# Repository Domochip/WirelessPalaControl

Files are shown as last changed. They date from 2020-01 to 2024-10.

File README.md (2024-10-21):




# WPalaControl

This project uses "Palazzetti library" and a D1 Mini to control Fumis based stove.  
It allows to power On/Off, change the setPoint, change fans speed, get status/alarms/temperatures of the stove.

Native HTTP requests are available which make is fully compatible with all existing Palazzetti/Fumis home automation plugins/apps.

Additionally, this project add MQTT protocol to monitor/control your stove in a much more efficient way.

## Stove Compatibility

Fumis Controller is used by many manufacturer for their stoves.
Here is a non-exhaustive list:  
  
Palazzetti / Jotul / TurboFonte / Godin / Fonte Flamme / Invicta / Casatelli / Alpis / Faizen / HETA / ...

If you have this control panel and/or controller in your stove, it's compatible.  
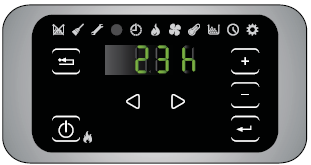
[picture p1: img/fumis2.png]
Fumis Controller
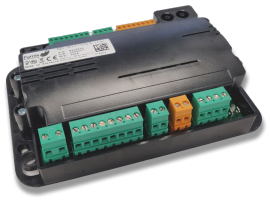
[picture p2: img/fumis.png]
Fumis Controller


## Home Automation compatibility

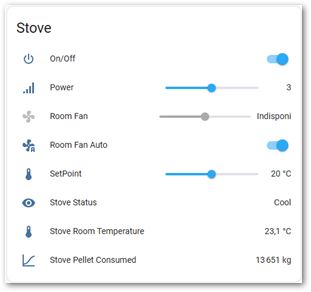
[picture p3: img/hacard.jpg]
hacard
| Logo HASS | [MQTT Integration](https://www.home-assistant.io/integrations/mqtt/) (autodiscovery) |  |
| --- | --- | --- |
| Logo Jeedom | [Palazzetti plugin](https://www.jeedom.com/market/index.php?v=d&p=market_display&id=3104) | Jeedom widget |

## Make/Get your adapter

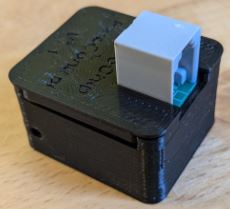
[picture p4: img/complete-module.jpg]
complete Module


🔧 If you want to build it yourself, you can find all details here : [BUILD](BUILD.md) 🔧  

🛍️🚀 Otherwise, I'm producing some small batches and offering it ready to use here : Tindie product (https://www.tindie.com/products/35770/)  

## Connect

⚠️ **You need to use a crossed RJ11 phone cable like this:** ⚠️  
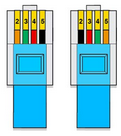
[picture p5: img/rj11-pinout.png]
WPalaControl rj11


Most of stove have an RJ11/RJ12 connector for PalaControl connection.  
If you don't have it, you need to cable it using a splitter to connect screen and PalaControl at the same time :  
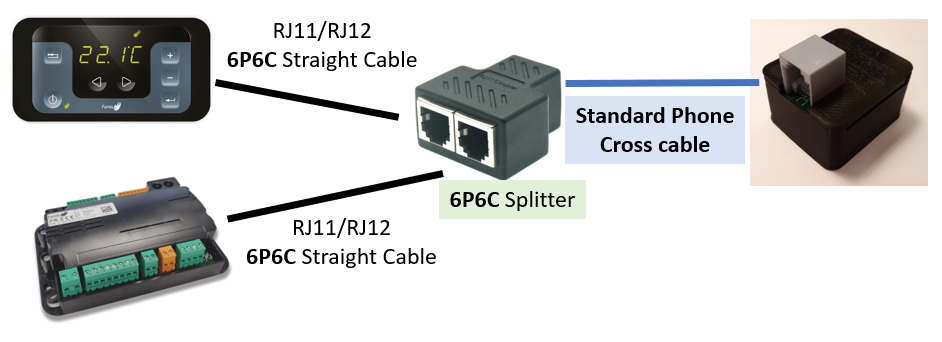
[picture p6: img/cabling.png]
WPalaControl cabling


Splitter and additional cable can be found on Aliexpress (search for "6p6c splitter" and "rj12 cable").  
The splitter should correspond to this small schematic :  
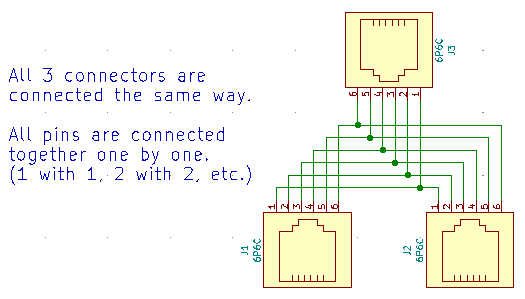
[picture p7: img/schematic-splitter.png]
WPalaControl schematic-splitter


## First Boot

During First Boot, the ESP boot in Access Point Mode

- Network SSID : `WirelessPalaControlXXXX`
- Password : `PasswordPalaControl`
- ESP URL : 👉 http://wpalacontrol.local 👈

Connect to this network and then configure it.

## Configuration pages

### Status

It returns you useful informations about the module and the stove.  
**The stove SN appears then 1 minute later, refreshed stove information appears (default upload period)**  
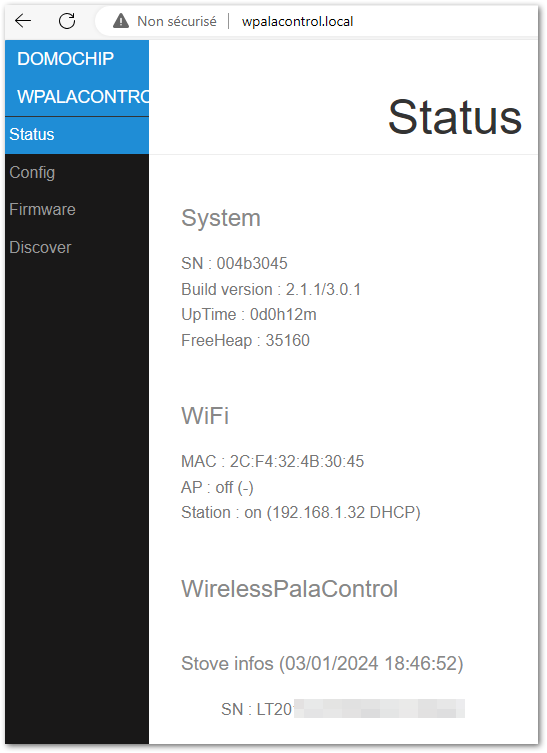
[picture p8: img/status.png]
status screenshot
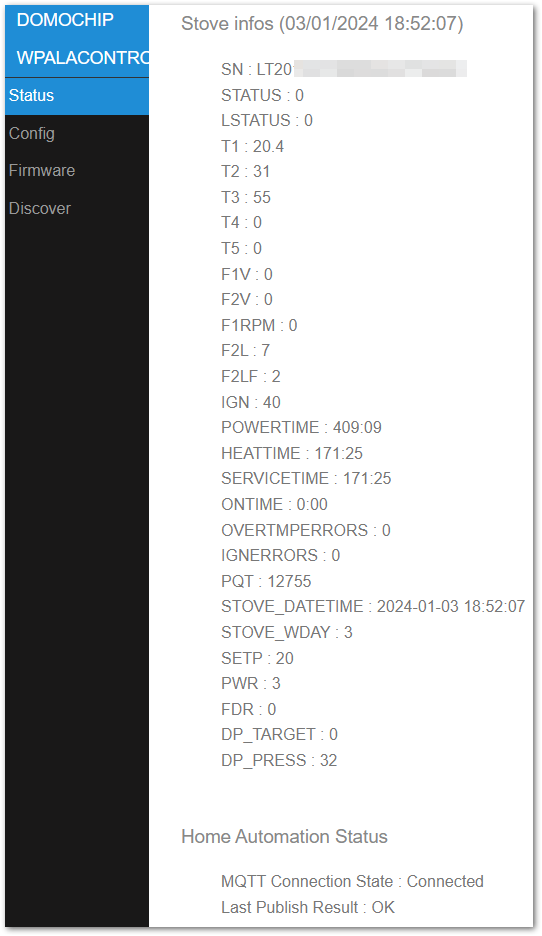
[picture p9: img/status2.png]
status2 screenshot


### Config

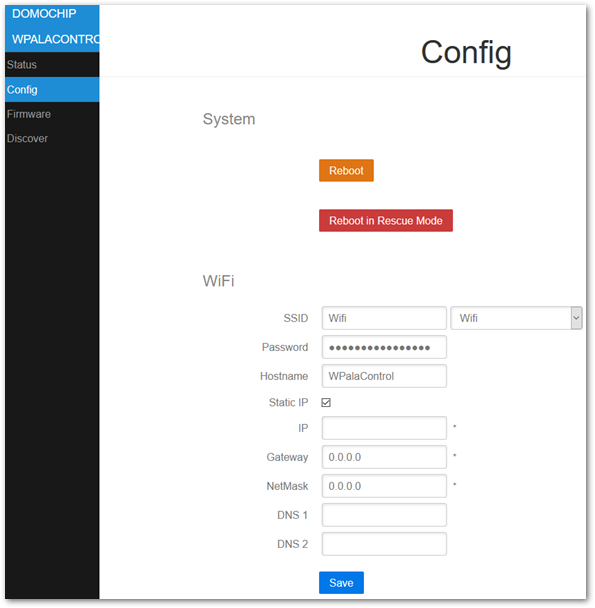
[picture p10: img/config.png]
config screenshot


#### System

- **Reboot**: restart the module
- **Reboot in Rescue Mode**: restart the module with default configuration

#### WiFi

- **ssid & password**: IDs of your Wifi Network  
- **hostname**: name of ESP on the network  
- **IP,GW,NetMask,DNS1&2**: Fixed IP configuration  

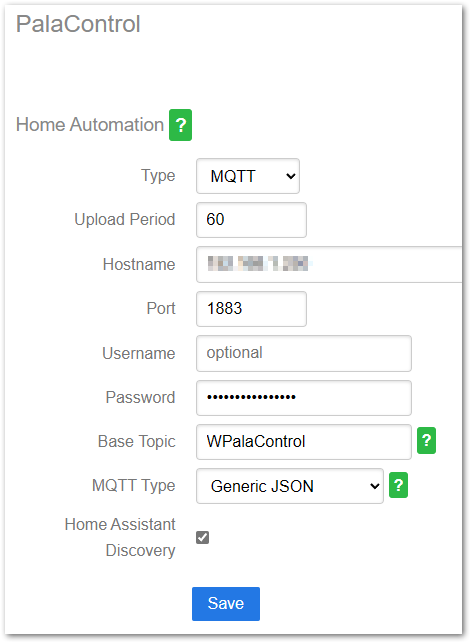
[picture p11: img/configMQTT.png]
configMQTT screenshot


#### PalaControl - Home Automation

- **Type**: enable/disable MQTT communication  
- **Upload Period**: delay between refresh of stove information (in seconds)  
- **Hostname,Port,Username,Password**: MQTT server infos (username and password are - optional)  
- **Base Topic**: prefix used for WPalaControl topic structure  
- **MQTT Type**: defines MQTT topics and data structure: 
  - **Generic**: publish raw values under the base topic (e.g. "{baseTopic}/T1" = "*20.00*")
  - **Generic JSON**: publish values JSON to "category" topic under base topic (e.g. "{baseTopic}/TMPS" = "*{"INFO":{"CMD":"GET TMPS","RSP":"OK......*")
  - **Generic Categorized**: publish raw values to "category" topic under base topic (e.g. "{baseTopic}/TMPS/T1" = "*20.00*")
- **Home Assistant Discovery**: Enable/disable Home Assistant auto-discovery

### Firmware

It allows you to flash a new firmware version using `WPalaControl.*.bin` file:  
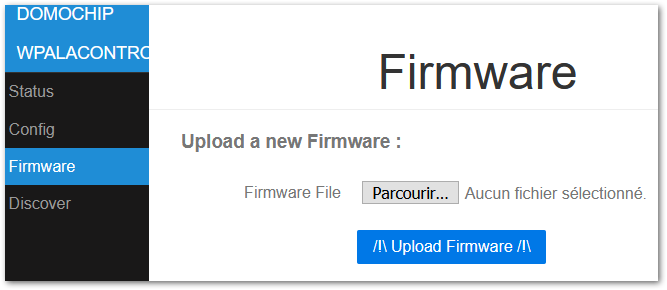
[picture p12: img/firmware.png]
firmware screenshot


## Use it

### HTTP

Natively, HTTP GET request can be sent directly to the module.  
Syntax:  **http://wpalacontrol.local/cgi-bin/sendmsg.lua?cmd={command}**

### MQTT

Commands can be sent via MQTT to %BaseTopic%**/cmd** topic once MQTT is configured.  
Execution result is:

- published following the configured MQTT Type
- published on %BaseTopic%**/result** in JSON format 

Module connection status is published to %BaseTopic%**/connected**:

- 0: not connected
- 1: Module connected but no communication with the stove
- 2: Module and stove connected

### Command List
  
- `GET+STDT`: get static data
- `GET+ALLS`: get all status data
- `GET+STAT`: get status of the stove⏲️
- `GET+TMPS`: get temperatures of the stove⏲️
- `GET+FAND`: get Fan values⏲️
- `GET+SETP`: get current Set Point (desired temperature)⏲️
- `GET+POWR`: get current power (1-5)⏲️
- `GET+CUNT`: get some counters
- `GET+CNTR`: get some counters (same as GET+CUNT)⏲️
- `GET+DPRS`: get delta pressure data⏲️
- `GET+TIME`: get stove clock data⏲️
- `GET+IOPT`: get IO ports status
- `GET+SERN`: get stove Serial Number
- `GET+MDVE`: get stove model and fw version
- `GET+CHRD`: get chrono data
- `GET+PARM+92`: get parameter (ex : 92=pellet type (1-3))
- `GET+HPAR+57`: get hidden parameter (ex : 57=% of pellet to feed for pellet type 3)
- `BKP+PARM+CSV`: get all parameters in a CSV file (HTTP only) ✨
- `BKP+PARM+JSON`: get all parameters in a JSON file (HTTP only) ✨
- `BKP+HPAR+CSV`: get all hidden parameters in a CSV file (HTTP only) ✨
- `BKP+HPAR+JSON`: get all hidden parameters in a JSON file (HTTP only) ✨
- `CMD+ON`: turn stove ON
- `CMD+OFF`: turn stove OFF
- `SET+POWR+3`: set power (1-5)
- `SET+PWRU`: increase power by 1 unit
- `SET+PWRD`: decrease power by 1 unit
- `SET+SETP+20`: set Set Point (desired temperature)
- `SET+STPF+19.8`: set Set Point with a 0.2° precision (depend of your stove model)✨
- `SET+STPU`: increase Set Point by 1 unit
- `SET+STPD`: decrease Set Point by 1 unit
- `SET+RFAN+7`: set Room Fan value (0-5;6=Max;7=Auto)
- `SET+FN2U`: increase Room Fan by 1 unit
- `SET+FN2D`: decrease Room Fan by 1 unit
- `SET+FN3L+0`: set Room Fan 3 value (0-5)
- `SET+FN4L+0`: set Room Fan 4 value (0-5)
- `SET+SLNT+0`: set Silent mode value (0-1)
- `SET+TIME+2023-12-28+19:42:00`: set stove Date and Time (2000-2099) (1-12) (1-31) (0-23) (0-59) (0-59)
- `SET+CSST+0`: set Chrono Status value (0-1)
- `SET+CSTH+2+18`: set Chrono Program Start Hour (1-6) (0-23)
- `SET+CSTM+2+30`: set Chrono Program Start Minute (1-6) (0-59)
- `SET+CSPH+2+22`: set Chrono Program Stop Hour (1-6) (0-23)
- `SET+CSPM+2+45`: set Chrono Program Stop Minute (1-6) (0-59)
- `SET+CSET+2+19`: set Chrono Program Set Point (1-6) (desired temperature)
- `SET+CDAY+7+3+6`: set Chrono Program for week day (Day-Mem-Prog) (1-7) (1-3) (1-6)
- `SET+CPRD+1+19+18+30+22+45`: set Chrono Program data (Prog-Temp-StartH-StartM-StopH-StopM) (1-6) (temperature) (0-23) (0-59) (0-23) (0-59)
- `SET+PARM+92+2`: set parameter 92 to value 2 (ex : 92=pellet type (1-3))
- `SET+HPAR+57+95`: set hidden parameter 57 to value 95 (ex : 57=% of pellet to feed for pellet type 3)

⏲️: Published automatically  
✨: WPalaControl specific commands

### Description

MQTT infos published every "Upload Period":

- `STATUS`: status of the stove
- `LSTATUS`: status of the stove
- `T1`, `T2`, `T3`, `T4`, `T5`: temperature of the stove
- `F1V`, `F2V`, `F2L`, `F2LF`, `F3L`, `F4L`: fan values (meaning depend of your stove model)
- `IGN`: ignition counter
- `IGNERRORS`: ignition error counter
- `POWERTIME`: total heating time (hour:minute)
- `HEATTIME`: ??? (hour:minute)
- `SERVICETIME`: heating time since last maintenance (hour:minute)
- `ONTIME`: time from last power ON (hour:minute)
- `OVERTMPERRORS`: overtemperature error counter
- `STOVE_DATETIME`: date of the stove
- `STOVE_WDAY`: week day of the stove
- `SETP`: current Set Point (desired temperature)
- `PQT`: wood pellet consumption
- `PWR`: current power (1-5)
- `FDR`: feeder
- `DP_TARGET`: delta pressure target
- `DP_PRESS`: actual delta pressure

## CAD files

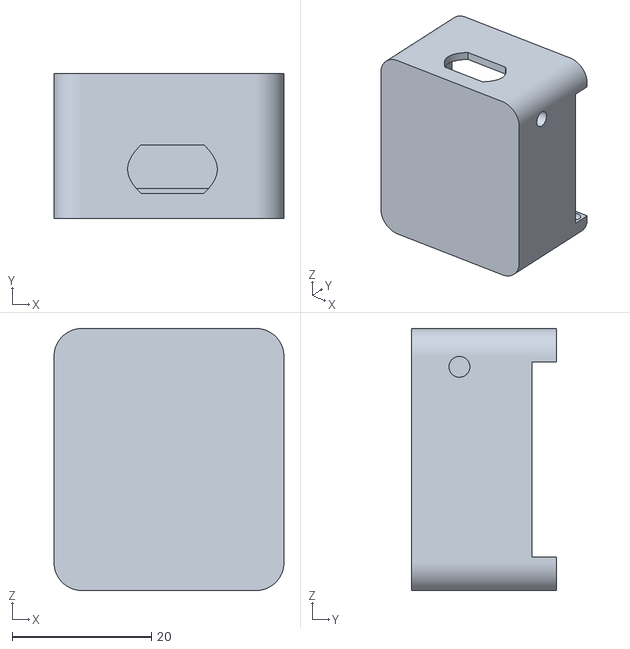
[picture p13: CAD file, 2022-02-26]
box/WirelessPalaControl Box.stl
33.0 x 20.8 x 37.6

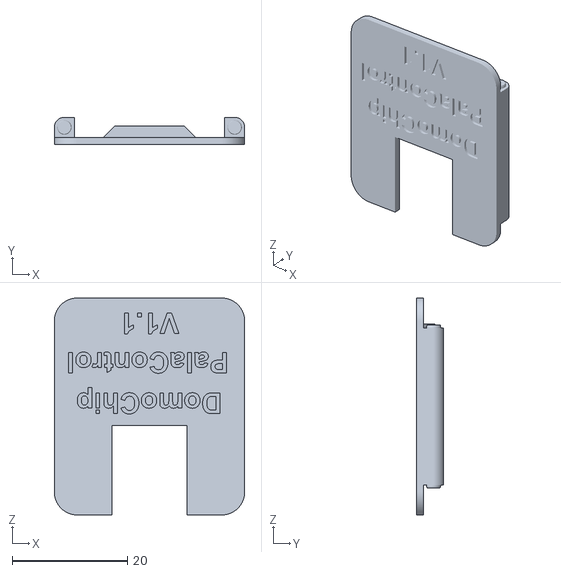
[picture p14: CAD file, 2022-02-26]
box/WirelessPalaControl Lid.stl
33.0 x 4.75 x 37.6

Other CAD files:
box/WirelessPalaControl v10.f3d

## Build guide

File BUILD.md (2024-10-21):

## Build your adapter

This adapter is designed to works with a D1 Mini (ESP8266) but it provides convenient header pins to use it with any other uController.

It is designed by Palazzetti using a Si8621 (Silicon Labs Isolator) to provide electrical isolation between uController and Stove electronic.  
This design uses exact same schematic and components.

### Schematic

All files are inside `schematic` subfolder and has been designed with KiCad (free and open source)  

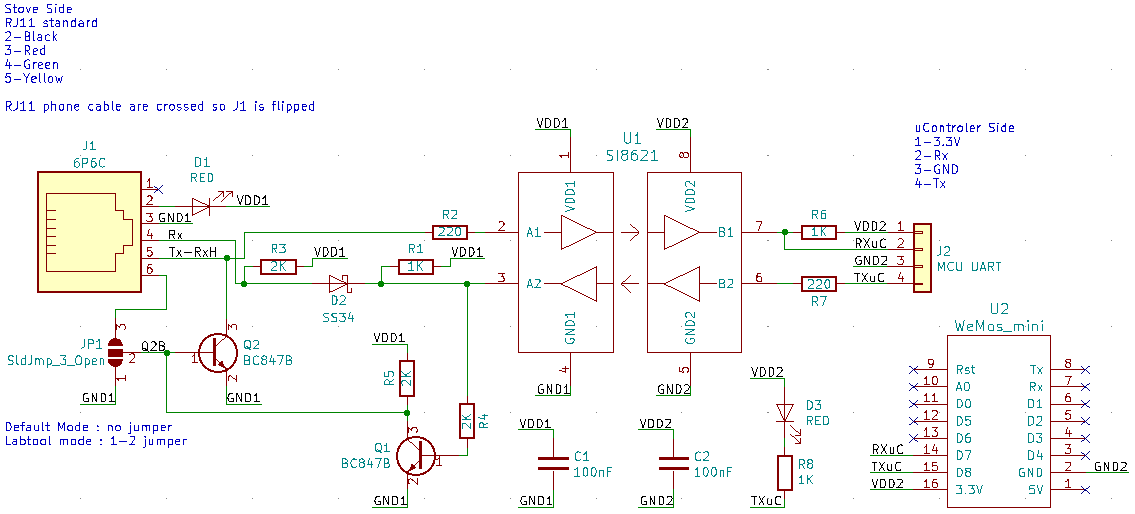
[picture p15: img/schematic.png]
WPalaControl schematic


### PCB

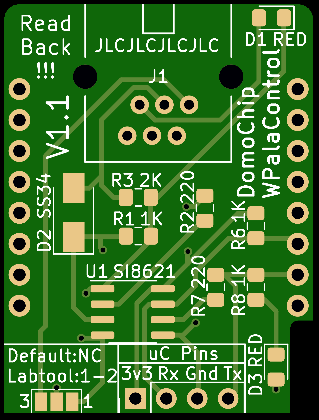
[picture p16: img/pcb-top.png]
WPalaControl PCB Top
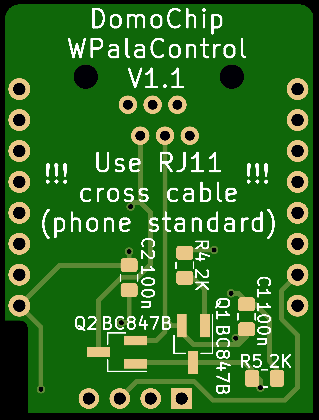
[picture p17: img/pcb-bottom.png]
WPalaControl PCB Bottom
  

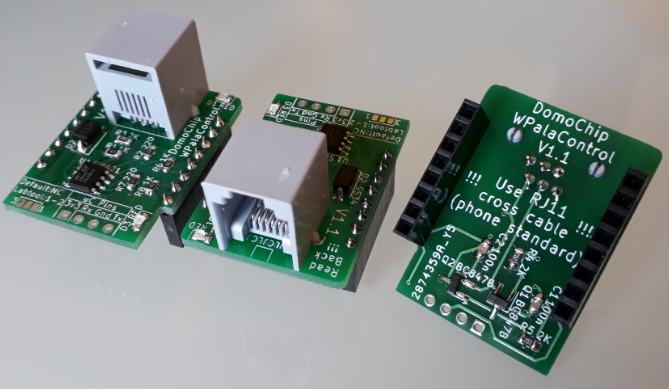
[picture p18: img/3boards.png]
WPalaControl 3boards
  

*I'm producing small batches of this adapter.*  
*If you are interested, you can find it here: [WPalacontrol on tindie](https://www.tindie.com/products/35770/)* 🛍️

### Box

Box project (Fusion 360 & STL) can be found into `box` folder

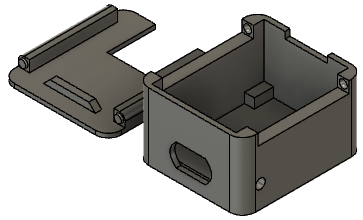
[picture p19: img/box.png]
WPalaControl box


### Firmware

Source code can be compiled using VSCode/PlatformIO and flashed onto a D1 Mini  
Or  
Download latest release in [Release section](https://github.com/Domochip/WPalaControl/releases)

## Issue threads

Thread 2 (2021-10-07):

MQTT and Domoticz

djpostka, 2021-10-07:
Bonjour,

J'ai un soucis pour raccordé la box sur Domoticz, en effet, ce dernier fonctionne avec un système d'IDX,
Pour associé les infos MQTT à mon device virtuel dans domoticz, il faut que le paramétré "IDX" soit intégré à la requête MQTT.

Tasmota ou espEasy offre la possibilité de déclaré l'IDX, serait-ce possible d'ajouter la cela aux paramètre MQTT ?

Merci par avance.

djpostka, 2021-10-09:
J'avoue ne pas vraiment savoir, je ne maitrise pas mqtt en dehors de configurer les clients/serveurs entre eux.
J'ai trouvé cette doc: https://www.domoticz.com/wiki/MQTT

J'ai trouvé ce projet si non qui est conçu pour fonctionner avec la CBOX, mais les commandes semble les même et en lua. Cependant, il n'est plus à jour et ma corrompu ma BDD domoticz sans trop savoir pourquoi.
https://github.com/kinou74/Domoticz-Palazzetti

Domochip, 2022-01-04:
Hello,

La dernière version du firmware rend le WPalaControl compatible.
L'utilisation des plugins conçus pour la CBox doivent maintenant fonctionner avec.
N'hésites pas à me redire si ton problème est solutionné.

djpostka, 2022-01-04:
Bonjour Merci beaucoup pour la mise à jour.
Le plus réussi à communiquer avec le poêle car il me remonte des valeurs correct, mais certaines ne le sont pas comme la vitesse du ventilateur, et je n'ai aucun contrôle sur le poêle (allumage, vitesse ventilateur...).

Voici les logs du plugins lors d'une tentative d'arrêt. Cela semble passé pourtant.

2022-01-05 00:01:08.087 WirelessPalaControl: (WirelessPalaControl) Sending 229 bytes of data
2022-01-05 00:01:08.087 WirelessPalaControl: (WirelessPalaControl) 47 45 54 20 2f 63 67 69 2d 62 69 6e 2f 73 65 6e 64 6d 73 67 GET./cgi-bin/sendmsg
2022-01-05 00:01:08.087 WirelessPalaControl: (WirelessPalaControl) 2e 6c 75 61 3f 63 6d 64 3d 43 4d 44 2b 4f 46 46 20 48 54 54 .lua?cmd=CMD+OFF.HTT
2022-01-05 00:01:08.087 WirelessPalaControl: (WirelessPalaControl) 50 2f 31 2e 31 0d 0a 43 6f 6e 74 65 6e 74 2d 54 79 70 65 3a P/1.1..Content-Type:
2022-01-05 00:01:08.087 WirelessPalaControl: (WirelessPalaControl) 20 74 65 78 74 2f 78 6d 6c 3b 20 63 68 61 72 73 65 74 3d 75 .text/xml;.charset=u
2022-01-05 00:01:08.087 WirelessPalaControl: (WirelessPalaControl) 74 66 2d 38 0d 0a 43 6f 6e 6e 65 63 74 69 6f 6e 3a 20 6b 65 tf-8..Connection:.ke
2022-01-05 00:01:08.087 WirelessPalaControl: (WirelessPalaControl) 65 70 2d 61 6c 69 76 65 0d 0a 41 63 63 65 70 74 3a 20 43 6f ep-alive..Accept:.Co
2022-01-05 00:01:08.087 WirelessPalaControl: (WirelessPalaControl) 6e 74 65 6e 74 2d 54 79 70 65 3a 20 74 65 78 74 2f 68 74 6d ntent-Type:.text/htm
2022-01-05 00:01:08.088 WirelessPalaControl: (WirelessPalaControl) 6c 3b 20 63 68 61 72 73 65 74 3d 55 54 46 2d 38 0d 0a 48 6f l;.charset=UTF-8..Ho
2022-01-05 00:01:08.088 WirelessPalaControl: (WirelessPalaControl) 73 74 3a 20 31 39 32 2e 31 36 38 2e 31 2e 31 35 30 3a 38 30 st:.192.168.1.150:80
2022-01-05 00:01:08.088 WirelessPalaControl: (WirelessPalaControl) 0d 0a 55 73 65 72 2d 41 67 65 6e 74 3a 20 44 6f 6d 6f 74 69 ..User-Agent:.Domoti
2022-01-05 00:01:08.088 WirelessPalaControl: (WirelessPalaControl) 63 7a 2f 31 2e 30 0d 0a 43 6f 6e 74 65 6e 74 2d 4c 65 6e 67 cz/1.0..Content-Leng
2022-01-05 00:01:08.088 WirelessPalaControl: (WirelessPalaControl) 74 68 3a 20 30 0d 0a 0d 0a .. .. .. .. .. .. .. .. .. .. .. th:.0....
2022-01-05 00:01:08.062 Status: User: Admin (IP: 192.168.1.27) initiated a switch command (76/WirelessPalaControl - On-Off/Off)

2022-01-05 00:01:31.098 WirelessPalaControl: (WirelessPalaControl) Sending 230 bytes of data
2022-01-05 00:01:31.098 WirelessPalaControl: (WirelessPalaControl) 47 45 54 20 2f 63 67 69 2d 62 69 6e 2f 73 65 6e 64 6d 73 67 GET./cgi-bin/sendmsg
2022-01-05 00:01:31.098 WirelessPalaControl: (WirelessPalaControl) 2e 6c 75 61 3f 63 6d 64 3d 47 45 54 2b 41 4c 4c 53 20 48 54 .lua?cmd=GET+ALLS.HT
2022-01-05 00:01:31.099 WirelessPalaControl: (WirelessPalaControl) 54 50 2f 31 2e 31 0d 0a 43 6f 6e 74 65 6e 74 2d 54 79 70 65 TP/1.1..Content-Type
2022-01-05 00:01:31.099 WirelessPalaControl: (WirelessPalaControl) 3a 20 74 65 78 74 2f 78 6d 6c 3b 20 63 68 61 72 73 65 74 3d :.text/xml;.charset=
2022-01-05 00:01:31.099 WirelessPalaControl: (WirelessPalaControl) 75 74 66 2d 38 0d 0a 43 6f 6e 6e 65 63 74 69 6f 6e 3a 20 6b utf-8..Connection:.k
2022-01-05 00:01:31.099 WirelessPalaControl: (WirelessPalaControl) 65 65 70 2d 61 6c 69 76 65 0d 0a 41 63 63 65 70 74 3a 20 43 eep-alive..Accept:.C
2022-01-05 00:01:31.099 WirelessPalaControl: (WirelessPalaControl) 6f 6e 74 65 6e 74 2d 54 79 70 65 3a 20 74 65 78 74 2f 68 74 ontent-Type:.text/ht
2022-01-05 00:01:31.099 WirelessPalaControl: (WirelessPalaControl) 6d 6c 3b 20 63 68 61 72 73 65 74 3d 55 54 46 2d 38 0d 0a 48 ml;.charset=UTF-8..H
2022-01-05 00:01:31.099 WirelessPalaControl: (WirelessPalaControl) 6f 73 74 3a 20 31 39 32 2e 31 36 38 2e 31 2e 31 35 30 3a 38 ost:.192.168.1.150:8
2022-01-05 00:01:31.099 WirelessPalaControl: (WirelessPalaControl) 30 0d 0a 55 73 65 72 2d 41 67 65 6e 74 3a 20 44 6f 6d 6f 74 0..User-Agent:.Domot
2022-01-05 00:01:31.099 WirelessPalaControl: (WirelessPalaControl) 69 63 7a 2f 31 2e 30 0d 0a 43 6f 6e 74 65 6e 74 2d 4c 65 6e icz/1.0..Content-Len
2022-01-05 00:01:31.100 WirelessPalaControl: (WirelessPalaControl) 67 74 68 3a 20 30 0d 0a 0d 0a .. .. .. .. .. .. .. .. .. .. gth:.0....

Domochip, 2022-01-04:
S'agit-il du plugin a cette adresse?
https://github.com/kinou74/Domoticz-Palazzetti

djpostka, 2022-01-04:
Oui, c'est bien celui ci

Domochip, 2022-01-05:
J'ai fait des tests de mon coté avec Domoticz et ce plugin.
Le plugin semble buggé malheureusement...
Concernant la temperature, il faut remplacer T5 par T1 dans le plugin.py (TMP_ROOM).
C'est T1 sur la majorité des poeles (sinon chercher MAINTPROBE dans le resultat d'une requete GET+STDT : 0 =>T1; 1=>T2; etc.)

Maintenant le plus gros problème se trouve concernant l'envoi des ordres, il ne fonctionne pas ou peu et crash la DB lorsque l'on redémarre Domoticz.
Si on lance un ordre dès le démarrage de Domoticz, il arrive bien, puis plus rien...
et si on redémarre Domoticz ensuite, DB KO/Domoticz HS :
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

djpostka, 2022-01-05:
Oui, le plugins n'est pas tout jeune et n'a pas reçu de mise à jour depuis un moment. Merci quand même, je vais continuer a utiliser mes script qui fonctionne pas trop mal.

Initialement, ma demande concernait surtout la demande d'un IDX MQTT, comme ont peut avoir sur Esp Easy par exemple

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

https://projetsdiy.fr/domoticz-materiel-capteurs-virtuels-espeasy/

Closed 2022-10-01.

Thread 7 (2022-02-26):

Wifi backup?

Flobul, 2022-02-26:
Sometimes, I reboot my wi-fi router and the Wpalacontrol does not reconnect to my router, it creates its own AP, and never try to reconnect. So I have to reset it manually. I notice only when I try to launch manually... So maybe a few days later.

Maybe adding a second SSID network (fallback)? I the first is unreachable, try the other one?
Or maybe a watchbog: if in AP because SSID network was unreachable, retry in 5 minutes?

Domochip, 2022-02-26:
Very strange, WirelessBase should look back for configured SSID every 60sec (during 20sec).
It does only if there is NO Client currently connected to the AP.
Is it your case?

Flobul, 2022-02-26:
No client connected to the WpalaControl AP.

carmelo42, 2022-08-30:
Same here, when the router is restarted, I can see the the Wpalacontrol AP, but even if no client is connected it does not reconnect to my router. I have to reboot Wpalacontrol.

Domochip, 2022-08-30:
please, ensure that no laptop or mobile phone connect to the module

carmelo42, 2022-08-31:
Yes, you were right ... I've forgotten a laptop used once to configure the module , my bad !
Sorry for the noise.

Flobul, 2022-11-11:
Nevermind, an old phone I used to configure WPalaControl was connecting to it...

Closed 2022-11-11.

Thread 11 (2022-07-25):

Platformio compilation error

carmelo42, 2022-07-25:
Hello !
Just downloaded the repo, and in VScode, on Mac and Linux, I got this :

```
> Executing task: platformio run --environment d1_mini <

Processing d1_mini (framework: arduino; board: d1_mini; platform: espressif8266)
-----------------------------------------------------------------------------------------------------------------------------------------------------------------------
Verbose mode can be enabled via `-v, --verbose` option

warning: Calling missing SConscript without error is deprecated.
Transition by adding must_exist=False to SConscript calls.
Missing SConscript 'src\base\data\prepare_webfiles.py'
File "/Users/carmelo/.platformio/penv/lib/python3.9/site-packages/platformio/builder/main.py", line 186, in <module>
CONFIGURATION: https://docs.platformio.org/page/boards/espressif8266/d1_mini.html
PLATFORM: Espressif 8266 (3.2.0) > WeMos D1 R2 and mini
HARDWARE: ESP8266 80MHz, 80KB RAM, 4MB Flash
PACKAGES:
 - framework-arduinoespressif8266 @ 3.30002.0 (3.0.2)
 - tool-esptool @ 1.413.0 (4.13)
 - tool-esptoolpy @ 1.30000.201119 (3.0.0)
 - toolchain-xtensa @ 2.100300.210717 (10.3.0)
LDF: Library Dependency Finder -> https://bit.ly/configure-pio-ldf
LDF Modes: Finder ~ chain, Compatibility ~ soft
Found 41 compatible libraries
Scanning dependencies...
Dependency Graph
|-- ESPAsyncTCP @ 1.2.2
|-- ESP Async WebServer @ 1.2.3
|   |-- ESPAsyncTCP @ 1.2.2
|   |-- Hash @ 1.0
|   |-- ESP8266WiFi @ 1.0
|   |-- ArduinoJson @ 6.19.4
|-- ESPAsyncUDP @ 0.0.0-alpha+sha.697c75a025
|-- ArduinoJson @ 6.19.4
|-- PubSubClient @ 2.8.0
|-- Palazzetti @ 2.1.0+sha.dc144fd
|-- EEPROM @ 1.0
|-- ESP8266WiFi @ 1.0
|-- LittleFS @ 0.1.0
|-- Ticker @ 1.0
Building in release mode
Compiling .pio/build/d1_mini/src/WirelessPalaControl.cpp.o
Compiling .pio/build/d1_mini/src/base/Application.cpp.o
Compiling .pio/build/d1_mini/src/base/Core.cpp.o
Compiling .pio/build/d1_mini/src/base/MQTTMan.cpp.o
Compiling .pio/build/d1_mini/src/base/Main.cpp.o
Compiling .pio/build/d1_mini/src/base/Utils.cpp.o
Compiling .pio/build/d1_mini/src/base/WifiMan.cpp.o
Generating LD script .pio/build/d1_mini/ld/local.eagle.app.v6.common.ld
In file included from src/base/WifiMan.cpp:1:
src/base/WifiMan.h:4:10: fatal error: ..\Main.h: No such file or directory

*****************************************************************
* Looking for ..\Main.h dependency? Check our library registry!
*
* CLI  > platformio lib search "header:..\Main.h"
* Web  > https://registry.platformio.org/search?q=header:..%5CMain.h
*
*****************************************************************

    4 | #include "..\Main.h"
      |          ^~~~~~~~~~~
In file included from src/base/MQTTMan.cpp:1:
src/base/MQTTMan.h:4:10: fatal error: ..\Main.h: No such file or directory

*****************************************************************
* Looking for ..\Main.h dependency? Check our library registry!
*
* CLI  > platformio lib search "header:..\Main.h"
* Web  > https://registry.platformio.org/search?q=header:..%5CMain.h
*
*****************************************************************

    4 | #include "..\Main.h"
      |          ^~~~~~~~~~~
compilation terminated.
compilation terminated.
In file included from src/base/Application.cpp:1:
src/base/Application.h:4:10: fatal error: ..\Main.h: No such file or directory

*****************************************************************
* Looking for ..\Main.h dependency? Check our library registry!
*
* CLI  > platformio lib search "header:..\Main.h"
* Web  > https://registry.platformio.org/search?q=header:..%5CMain.h
*
*****************************************************************

    4 | #include "..\Main.h"
      |          ^~~~~~~~~~~
In file included from src/base/Core.cpp:1:
src/base/Core.h:4:10: fatal error: ..\Main.h: No such file or directory

*****************************************************************
* Looking for ..\Main.h dependency? Check our library registry!
*
* CLI  > platformio lib search "header:..\Main.h"
* Web  > https://registry.platformio.org/search?q=header:..%5CMain.h
*
*****************************************************************

    4 | #include "..\Main.h"
      |          ^~~~~~~~~~~
compilation terminated.
compilation terminated.
*** [.pio/build/d1_mini/src/base/WifiMan.cpp.o] Error 1
*** [.pio/build/d1_mini/src/base/Core.cpp.o] Error 1
*** [.pio/build/d1_mini/src/base/Application.cpp.o] Error 1
*** [.pio/build/d1_mini/src/base/MQTTMan.cpp.o] Error 1
In file included from src/WirelessPalaControl.cpp:1:
src/WirelessPalaControl.h:5:10: fatal error: base\Utils.h: No such file or directory

********************************************************************
* Looking for base\Utils.h dependency? Check our library registry!
*
* CLI  > platformio lib search "header:base\Utils.h"
* Web  > https://registry.platformio.org/search?q=header:base%5CUtils.h
*
********************************************************************

    5 | #include "base\Utils.h"
      |          ^~~~~~~~~~~~~~
compilation terminated.
*** [.pio/build/d1_mini/src/WirelessPalaControl.cpp.o] Error 1
src/base/Main.cpp:12:10: fatal error: ..\Main.h: No such file or directory

*****************************************************************
* Looking for ..\Main.h dependency? Check our library registry!
*
* CLI  > platformio lib search "header:..\Main.h"
* Web  > https://registry.platformio.org/search?q=header:..%5CMain.h
*
*****************************************************************

   12 | #include "..\Main.h"
      |          ^~~~~~~~~~~
compilation terminated.
*** [.pio/build/d1_mini/src/base/Main.cpp.o] Error 1
===================================================================== [FAILED] Took 1.96 seconds =====================================================================
The terminal process "platformio 'run', '--environment', 'd1_mini'" terminated with exit code: 1.

Terminal will be reused by tasks, press any key to close it.

```

I know I can use the released file, but I like to understand why it fail ;)

Flobul, 2022-07-25:
Prefer windows to compile it.

Directories used in the program are not well recognized in linux/Mac OS.

carmelo42, 2022-07-26:
Thanks !
I don't have any Windows machine available, I will then rely on binary releases ;)

Domochip, 2023-12-29:
Code has been updated to be compiled on non-Windows machine.

carmelo42, 2023-12-29:
Thanks :)

Happy to see this project is still updated :)

Closed 2022-07-26.

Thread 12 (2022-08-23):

D1 Mini communication

KaktuMAN, 2022-08-23:
Hi,
After flashing the ESP8266, everything worked properly, I was able to run PalaControl. But at the moment I attach the ESP to the PCB, nothing happens, I'm unable to start the web ui.
It seems that it's the TX pin that is the source of the problem, do you have an idea of why it's not working ?

Domochip, 2022-08-23:
You need to connect it to your stove. Otherwise some timeout occurs and the module keeps rebooting undefinitly

KaktuMAN, 2022-08-23:
I think it was that, but now the stove give me the error 004 and I still don't have access to the web UI

KaktuMAN, 2022-08-23:
And also, the ESP just blink once

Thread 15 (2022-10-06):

Configuration and infos on TIMER status

1300371, 2022-10-06:
Hello,

I've got a Palazzetti stove and there is a TIMER fonction that you have to turn on if you want to schedule ON/oFF.

Is there a way to get that _TIMER status_ and also to set it ?

Here is a video of the feature: https://www.youtube.com/watch?v=YBgKCtgVSOY

Domochip, 2022-10-06:
Hi, I never used it, but I think this is `Chrono Data`/`Chrono Status` that you are looking for.
And `Chrono Program` is the way to configure its planning.

1300371, 2022-10-06:
BTW, is it possible to forward more data via mqtt ? All these data are availble only via http ? 😕

1300371, 2022-10-10:
Ping @Domochip

1300371, 2022-10-24:
Did read you my second question @Domochip ? Sorry for spam

Domochip, 2023-12-28:
Hello,
Sorry for the very very late reply.
The new V3.0.0 (just released) allows you to get this info via MQTT if you send "GET+CHRD" to cmd topic.
Could you give it a try and let me know if it matches to your needs?

1300371, 2023-12-29:
No problem.
To update, just have to upload the _bin_ firmware file througth the UI ?

Domochip, 2023-12-29:
yes

Domochip, 2024-01-30:
Ping @1300371

1300371, 2024-01-30:
Sorry 😅
As this is winter in France, I want to wait spring to not jeopardize my installation (in case of something goes wrong)

Closed 2024-02-18.

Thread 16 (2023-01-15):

Any chance update code for ESP32 ?

Flobul, 2023-01-15:
Hi.

Sorry to bother, but is there any chance you update this repo for another hardware plateform? (espressif32 instead of espressif8266)
Or maybe a way to use the lib with another system (tasmota, espeasy...)

Domochip, 2023-01-15:
Hi,

mm, regading other systems, it is difficult to respect right timing and listen on UDP + TCP + Web like official box.

For ESP32, I tried a few years ago to port it but Ticker class was missing. It seems to exists now and this option seems possible.
ESP32 Mini are still larger than D1Mini and cost a little more so the right question is Why? Do you see a particular improvement?

Domochip, 2024-09-04:
Hello,

code has been adapted to ESP32 on test-esp32 branch

Domochip, 2024-09-04:
And tested successfully on my side

Flobul, 2024-09-23:
Thank you! Nice job.

I made it work but got some compiling errors in ESP8266:
```
Compiling .pio/build/d1_mini/lib359/ESP8266WiFi/WiFiServerSecureAxTLS.cpp.o
Indexing .pio/build/d1_mini/lib64f/libPubSubClient.a
In file included from src/base/Application.cpp:1:0:
src/base/Application.cpp: In lambda function:
src/base/Application.h:9:41: error: 'using ESP8266WebServer = class esp8266webserver::ESP8266WebServerTemplate<WiFiServer>' has no member named 'keepAlive'
 #define SERVER_KEEPALIVE_FALSE() server.keepAlive(false);
                                         ^
src/base/Application.cpp:165:5: note: in expansion of macro 'SERVER_KEEPALIVE_FALSE'
     SERVER_KEEPALIVE_FALSE()
     ^
src/base/Application.cpp: In lambda function:
src/base/Application.h:9:41: error: 'using ESP8266WebServer = class esp8266webserver::ESP8266WebServerTemplate<WiFiServer>' has no member named 'keepAlive'
 #define SERVER_KEEPALIVE_FALSE() server.keepAlive(false);
                                         ^
src/base/Application.cpp:173:5: note: in expansion of macro 'SERVER_KEEPALIVE_FALSE'
     SERVER_KEEPALIVE_FALSE()
     ^
src/base/Application.cpp: In lambda function:
src/base/Application.h:9:41: error: 'using ESP8266WebServer = class esp8266webserver::ESP8266WebServerTemplate<WiFiServer>' has no member named 'keepAlive'
 #define SERVER_KEEPALIVE_FALSE() server.keepAlive(false);
```

```
Compiling .pio/build/d1_mini/FrameworkArduino/core_esp8266_waveform_pwm.cpp.o
src/WirelessPalaControl.cpp: In member function 'bool WebPalaControl::executePalaCmd(const String&, String&, bool)':
src/WirelessPalaControl.cpp:933:28: error: 'class ESP8266WiFiClass' has no member named 'getHostname'
       data["LABEL"] = WiFi.getHostname();
                            ^
Compiling .pio/build/d1_mini/FrameworkArduino/core_esp8266_wiring.cpp.o
src/WirelessPalaControl.cpp:951:28: error: 'class ESP8266WiFiClass' has no member named 'broadcastIP'
       data["WBCST"] = WiFi.broadcastIP().toString();
```

```
src/WirelessPalaControl.cpp: In member function 'bool WebPalaControl::executePalaCmd(const String&, String&, bool)':
src/WirelessPalaControl.cpp:933:28: error: 'class ESP8266WiFiClass' has no member named 'getHostname'
       data["LABEL"] = WiFi.getHostname();
                            ^
src/WirelessPalaControl.cpp:951:28: error: 'class ESP8266WiFiClass' has no member named 'broadcastIP'
       data["WBCST"] = WiFi.broadcastIP().toString();
                            ^
```

Here are the changes I made to "fix" it:
https://github.com/Flobul/WirelessPalaControl/pull/3/files

Domochip, 2024-09-23:
everything has been merged on WPalaControl master branch and I'm able to compile ESP32 version by just switching to the esp32 env:
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

Do you have a different result?

Flobul, 2024-09-23:
esp8266 (KO):
```
 *  Exécution de la tâche : platformio run

Processing d1_mini (framework: arduino; board: d1_mini; platform: espressif8266)
-------------------------------------------------------------------------------------------------------------------------------------------------------
Library Manager: Installing domochip/Palazzetti#v2.7.3
Unpacking  [####################################]  100%
Library Manager: Palazzetti@2.7.3 has been installed!
Verbose mode can be enabled via `-v, --verbose` option
---- Copying base files ----
----------------------------
--- Converting web files ---
----------------------------
CONFIGURATION: https://docs.platformio.org/page/boards/espressif8266/d1_mini.html
PLATFORM: Espressif 8266 (2023.4.0) > WeMos D1 R2 and mini
HARDWARE: ESP8266 80MHz, 80KB RAM, 4MB Flash
PACKAGES:
 - framework-arduinoespressif8266 @ 2.7.4+9
 - tool-esptoolpy @ 1.40501.0 (4.5.1)
 - toolchain-xtensa @ 2.40802.200502 (4.8.2)
LDF: Library Dependency Finder -> https://bit.ly/configure-pio-ldf
LDF Modes: Finder ~ chain, Compatibility ~ soft
Library Manager: Installing domochip/Palazzetti#v2.7.3
Unpacking 0% 10% 20% 30% 40% 50% 60% 70% 80%
Library Manager: Palazzetti@2.7.3 has been installed!
Found 32 compatible libraries
Scanning dependencies...
Dependency Graph
|-- ArduinoJson @ 7.2.0
|-- PubSubClient @ 2.8.0
|-- EEPROM @ 1.0
|-- ESP8266WebServer @ 1.0
|-- ESP8266WiFi @ 1.0
|-- LittleFS(esp8266) @ 0.1.0
|-- Palazzetti @ 2.7.3
|-- Ticker @ 1.0
|-- ESP8266mDNS @ 1.2
Building in release mode
Compiling .pio/build/d1_mini/src/WirelessPalaControl.cpp.o
Compiling .pio/build/d1_mini/src/base/Application.cpp.o
Compiling .pio/build/d1_mini/src/base/Core.cpp.o
Compiling .pio/build/d1_mini/src/base/MQTTMan.cpp.o
Compiling .pio/build/d1_mini/src/base/Main.cpp.o
Compiling .pio/build/d1_mini/src/base/Utils.cpp.o
Compiling .pio/build/d1_mini/src/base/WifiMan.cpp.o
Generating LD script .pio/build/d1_mini/ld/local.eagle.app.v6.common.ld
Compiling .pio/build/d1_mini/lib075/PubSubClient/PubSubClient.cpp.o
Compiling .pio/build/d1_mini/lib248/EEPROM/EEPROM.cpp.o
Compiling .pio/build/d1_mini/lib359/ESP8266WiFi/BearSSLHelpers.cpp.o
Compiling .pio/build/d1_mini/lib359/ESP8266WiFi/CertStoreBearSSL.cpp.o
Compiling .pio/build/d1_mini/lib359/ESP8266WiFi/ESP8266WiFi.cpp.o
Compiling .pio/build/d1_mini/lib359/ESP8266WiFi/ESP8266WiFiAP.cpp.o
Compiling .pio/build/d1_mini/lib359/ESP8266WiFi/ESP8266WiFiGeneric.cpp.o
Compiling .pio/build/d1_mini/lib359/ESP8266WiFi/ESP8266WiFiGratuitous.cpp.o
Compiling .pio/build/d1_mini/lib359/ESP8266WiFi/ESP8266WiFiMulti.cpp.o
.pio/libdeps/d1_mini/PubSubClient/src/PubSubClient.cpp: In member function 'boolean PubSubClient::publish_P(const char*, const uint8_t*, unsigned int, boolean)':
.pio/libdeps/d1_mini/PubSubClient/src/PubSubClient.cpp:523:19: warning: comparison between signed and unsigned integer expressions [-Wsign-compare]
     return (rc == expectedLength);
                   ^
Compiling .pio/build/d1_mini/lib359/ESP8266WiFi/ESP8266WiFiSTA-WPS.cpp.o
Archiving .pio/build/d1_mini/lib248/libEEPROM.a
Compiling .pio/build/d1_mini/lib359/ESP8266WiFi/ESP8266WiFiSTA.cpp.o
Compiling .pio/build/d1_mini/lib359/ESP8266WiFi/ESP8266WiFiScan.cpp.o
Compiling .pio/build/d1_mini/lib359/ESP8266WiFi/WiFiClient.cpp.o
Compiling .pio/build/d1_mini/lib359/ESP8266WiFi/WiFiClientSecureAxTLS.cpp.o
In file included from src/base/Application.cpp:1:0:
src/base/Application.cpp: In lambda function:
src/base/Application.h:9:41: error: 'using ESP8266WebServer = class esp8266webserver::ESP8266WebServerTemplate<WiFiServer>' has no member named 'keepAlive'
 #define SERVER_KEEPALIVE_FALSE() server.keepAlive(false);
                                         ^
src/base/Application.cpp:165:5: note: in expansion of macro 'SERVER_KEEPALIVE_FALSE'
     SERVER_KEEPALIVE_FALSE()
     ^
src/base/Application.cpp: In lambda function:
src/base/Application.h:9:41: error: 'using ESP8266WebServer = class esp8266webserver::ESP8266WebServerTemplate<WiFiServer>' has no member named 'keepAlive'
 #define SERVER_KEEPALIVE_FALSE() server.keepAlive(false);
                                         ^
src/base/Application.cpp:173:5: note: in expansion of macro 'SERVER_KEEPALIVE_FALSE'
     SERVER_KEEPALIVE_FALSE()
     ^
src/base/Application.cpp: In lambda function:
src/base/Application.h:9:41: error: 'using ESP8266WebServer = class esp8266webserver::ESP8266WebServerTemplate<WiFiServer>' has no member named 'keepAlive'
 #define SERVER_KEEPALIVE_FALSE() server.keepAlive(false);
                                         ^
src/base/Application.cpp:181:5: note: in expansion of macro 'SERVER_KEEPALIVE_FALSE'
     SERVER_KEEPALIVE_FALSE()
     ^
src/base/Application.cpp: In lambda function:
src/base/Application.h:9:41: error: 'using ESP8266WebServer = class esp8266webserver::ESP8266WebServerTemplate<WiFiServer>' has no member named 'keepAlive'
 #define SERVER_KEEPALIVE_FALSE() server.keepAlive(false);
                                         ^
src/base/Application.cpp:189:5: note: in expansion of macro 'SERVER_KEEPALIVE_FALSE'
     SERVER_KEEPALIVE_FALSE()
     ^
src/base/Application.cpp: In lambda function:
src/base/Application.h:9:41: error: 'using ESP8266WebServer = class esp8266webserver::ESP8266WebServerTemplate<WiFiServer>' has no member named 'keepAlive'
 #define SERVER_KEEPALIVE_FALSE() server.keepAlive(false);
                                         ^
src/base/Application.cpp:197:5: note: in expansion of macro 'SERVER_KEEPALIVE_FALSE'
     SERVER_KEEPALIVE_FALSE()
     ^
src/base/Application.cpp: In lambda function:
src/base/Application.h:9:41: error: 'using ESP8266WebServer = class esp8266webserver::ESP8266WebServerTemplate<WiFiServer>' has no member named 'keepAlive'
 #define SERVER_KEEPALIVE_FALSE() server.keepAlive(false);
                                         ^
src/base/Application.cpp:205:5: note: in expansion of macro 'SERVER_KEEPALIVE_FALSE'
     SERVER_KEEPALIVE_FALSE()
     ^
src/base/Application.cpp: In lambda function:
src/base/Application.h:9:41: error: 'using ESP8266WebServer = class esp8266webserver::ESP8266WebServerTemplate<WiFiServer>' has no member named 'keepAlive'
 #define SERVER_KEEPALIVE_FALSE() server.keepAlive(false);
                                         ^
src/base/Application.cpp:221:7: note: in expansion of macro 'SERVER_KEEPALIVE_FALSE'
       SERVER_KEEPALIVE_FALSE()
       ^
src/base/Application.h:9:41: error: 'using ESP8266WebServer = class esp8266webserver::ESP8266WebServerTemplate<WiFiServer>' has no member named 'keepAlive'
 #define SERVER_KEEPALIVE_FALSE() server.keepAlive(false);
                                         ^
src/base/Application.cpp:226:7: note: in expansion of macro 'SERVER_KEEPALIVE_FALSE'
       SERVER_KEEPALIVE_FALSE()
       ^
In file included from src/base/Core.h:5:0,
                 from src/base/Core.cpp:1:
src/base/Core.cpp: In lambda function:
src/base/Application.h:9:41: error: 'using ESP8266WebServer = class esp8266webserver::ESP8266WebServerTemplate<WiFiServer>' has no member named 'keepAlive'
 #define SERVER_KEEPALIVE_FALSE() server.keepAlive(false);
                                         ^
src/base/Core.cpp:84:5: note: in expansion of macro 'SERVER_KEEPALIVE_FALSE'
     SERVER_KEEPALIVE_FALSE()
     ^
Archiving .pio/build/d1_mini/lib075/libPubSubClient.a
src/base/Core.cpp: In lambda function:
src/base/Application.h:9:41: error: 'using ESP8266WebServer = class esp8266webserver::ESP8266WebServerTemplate<WiFiServer>' has no member named 'keepAlive'
 #define SERVER_KEEPALIVE_FALSE() server.keepAlive(false);
                                         ^
src/base/Core.cpp:103:5: note: in expansion of macro 'SERVER_KEEPALIVE_FALSE'
     SERVER_KEEPALIVE_FALSE()
     ^
src/base/Core.cpp: In lambda function:
src/base/Application.h:9:41: error: 'using ESP8266WebServer = class esp8266webserver::ESP8266WebServerTemplate<WiFiServer>' has no member named 'keepAlive'
 #define SERVER_KEEPALIVE_FALSE() server.keepAlive(false);
                                         ^
src/base/Core.cpp:118:5: note: in expansion of macro 'SERVER_KEEPALIVE_FALSE'
     SERVER_KEEPALIVE_FALSE()
     ^
src/base/Core.cpp: In lambda function:
src/base/Application.h:9:41: error: 'using ESP8266WebServer = class esp8266webserver::ESP8266WebServerTemplate<WiFiServer>' has no member named 'keepAlive'
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

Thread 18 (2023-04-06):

Stove infos

Ir0n42, 2023-04-06:
Hi, I have received my controller with 1.4.1 system running.
I have configured it on my network and plug RJ11 on my Palazzetti Monica.
But now, stove info still empty, why? Forgot something?
Thank you

Domochip, 2023-04-06:
Hi,
Could you provide a screenshot of the complete version number.
maybe a picture of the cabling to the stove too.

Thanks

Ir0n42, 2023-04-06:
Yes sure!
![Uploading 97B386A4-6BAB-4EED-9DDF-948B14A84888.jpeg…]()

Ir0n42, 2023-04-06:
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

Ir0n42, 2023-04-06:
![Uploading C96A8E17-DF64-4DAE-9256-6EED3C5654E1.jpeg…]()

Ir0n42, 2023-04-06:
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

Ir0n42, 2023-04-06:
![Uploading D22D207B-CF5C-4F3B-B3B8-6D90F3F0F87A.jpeg…]()

Ir0n42, 2023-04-06:
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

Ir0n42, 2023-04-06:
![Uploading 63EA6B6D-D54F-4FF6-88C7-643DC2CC7C92.jpeg…]()

Ir0n42, 2023-04-06:
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

Domochip, 2023-04-07:
OK,
First I advise to update to the last firmware version.
Next to this one, you should see serial number on the landing page.
With your current version, even if nothing appears, it doesn't mean the module doesn't work.
You can try to query this URL to check : http://**{IP}**/cgi-bin/sendmsg.lua?cmd=GET+STDT

Ir0n42, 2023-04-07:
Ok thank you, I have update it.
Message :
 Stove infos (07/04/2023 10:02:30)
    MSG : Stove communication failed! please check cabling to your stove.
And when I Go to http://{IP}/cgi-bin/sendmsg.lua?cmd=GET+STDT
Message :
{"INFO":{"CMD":"GET STDT","MSG":"Stove communication failed","RSP":"TIMEOUT"},"SUCCESS":false,"DATA":{"NODATA":true}}

Domochip, 2023-04-07:
It seems you have an issue with the cabling.
Does the cable match with the image here ? : https://github.com/Domochip/WirelessPalaControl#connect

Ir0n42, 2023-04-07:
Yes ! It's crossed

Domochip, 2023-04-07:
Then, do you have a picture of your stove motherboard?

Ir0n42, 2023-04-07:
I will open it

Ir0n42, 2023-04-07:
That enouth for you?
![Uploading F349A479-4C50-4215-ADFB-769DBD368CD2.jpeg…]()

Ir0n42, 2023-04-07:
@
![Uploading 18DE64C0-0DCA-4E64-BA39-E1F6593D57F0.jpeg…]()

Ir0n42, 2023-04-07:
![Uploading BB2FE962-0CBC-43A3-BE78-15FA04A11DB2.jpeg…]()

Ir0n42, 2023-04-07:
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

Domochip, 2023-04-07:
Yes, defenitly!
This is a MicroNova motherboard and WirelessPalaControl is **NOT** compatible with MicroNova.
As per written in first chapters (https://github.com/Domochip/WirelessPalaControl), this project aims to control Fumis based stoves.
Your stove should be pretty old to have this kind of Motherboard.

I let you contact me by mail for further discussion.

Closed 2023-04-07.

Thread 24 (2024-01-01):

Status feedback slower than in earlier versions?

sven337, 2024-01-01:
I have not bisected this but, I seem to recall that when I sent CMD +ON to start the stove, I would get immediate status feedback over MQTT.
This was with the firmware you shipped me recently, which I upgraded to 2.1.1/3.0.0.

Now, it seems I have to wait for the next publishTick.
Is this a known consequence of the refactoring?

I would very much appreciate to see the status reflected as soon as it changes, and I think it used to work like that.
Thanks

Domochip, 2024-01-02:
thanks for your feedback.
It was a missing return in Palazzetti Lib (switchOff/On functions).
I've implemented it and use it now in WPalaControl.
The current repo version should solve the problem.
I will release it shortly but feel free to compile and use it now if you need ;-)

sven337, 2024-01-02:
Seems like it's stuck in a reboot loop with that version. I need to investigate.

Domochip, 2024-01-02:
Arg, sorry.
Yes, you can connect it using a micro-usb cable and flash it using VSCode/PlatformIO.
I'll have a look shortly

sven337, 2024-01-02:
Indeed, I just did so (esptool.py write_flash 0x0 /tmp/WirelessPalaControl.v2.1.1-3.0.0.bin), and it's back to normal.
So it seems there's something wrong with your change, but it's not obvious to me what it could be.

Domochip, 2024-01-02:
thanks, I just fixed it :-)

Domochip, 2024-01-02:
I'm back regarding the Status feedback.
I was able to compile and run it without any particular issue. Does libraries are up to date on your side? Which OS are you using?
Anyway, the test is "failing" because Palazzetti lib is now going too fast :-D and returned STATUS is not the "final" one.
I mean when I power ON the stove and temperature is bellow the threshold, it should end up to STATUS 9.
But I'm receiving STATUS 3, which is a transient step to 9...
I'll add a delay before reading of Status to return.

sven337, 2024-01-02:
I am pretty sure that before v2.1.1/3.0.0 the status would update more or less right away. I would click "ON" in home assistant (which I've hooked up to send CMD+ON), and receive a MQTT status update to HEATUP = 9 within 1-2 seconds.

I build on Linux, libraries are up-to-date as far as I know (platformio handles that, right?).

My suggestion, don't add a delay, instead reset the next publishTick so it happens earlier?

Domochip, 2024-01-02:
PlatformIO doesn't update libraries because I didn't specified version for ArduinoJson and PubSubClient. Another point to improve... (maybe also for ESP8266 Arduino version).

The delay will be applied only to CMD+ON/OFF commands.
The whole publishTick is not required for powering on/off the stove. And anyway, lib Palazzetti is now so fast that I'm not sure this will solve the problem :-D
I'm currently testing it.

Domochip, 2024-01-02:
A delay of 500ms is working on my side, but I will do a test session to measure it more precisely. Then I'll be able to apply a "safety" margin

Domochip, 2024-01-04:
OK, I did some tests yesterday on my stove.

Stove ON (send switchOff command):
 - not heating nor fan : STATUS 9->0 took 89ms (3rd getStatus)
 - no fire but FAN is cooling : STATUS 9->10 took 37ms (1st getStatus)
 - heating : STATUS 6->10 took 63ms (2nd getStatus)

Sove OFF (send switchON command):
 - SETP is 2°C under the T1 (no need to heat) : STATUS 0->3 took 37ms (1st getStatus) THEN 3->9 took 305ms (10th getStatus)
 - SETP is above T1 (will heat) : STATUS 0->3 took 37ms AND after 1.2s STATUS is still equals to 3. Stove switch to 4 later after some check etc.

Conclusion :
 - for switchOff, a delay of 200ms should be OK (max measured is 89ms)
 - for switchOn, a delay of 500ms should be OK (max  is 305ms) (regarding the case where the stove need to heat, a STATUS=3 will then be returned and is a correct return value)

Domochip, 2024-01-04:
OK, the issue should be solved now using the latest release : https://github.com/Domochip/WirelessPalaControl/releases/tag/v2.1.2-3.0.2

Regarding compilation on your env : which distro do you use?

sven337, 2024-01-04:
Thank you, I confirm your latest changes fix the problem I was reporting, I now get immediate status updates again.

I build on Archlinux, but I don't think that should cause any problem. In fact I've just produced my own build with your latest change and it works. I don't know what happened but let's ignore it.

Thank you again for your support. By the way, my stove is a Casatelli Carlo.

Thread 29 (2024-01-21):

Set silent mode returns a timeout error

Flobul, 2024-01-21:
Hi.

When SET+SLNT+1 command is sent, the room fan stops, but the cmd returns a timeout issue.
When SET+SLNT+0 command is sent, nothing happens (is it supposed to recover last fan value ?)

```
Mac@Flobul % curl "http://192.168.XXX.XXX/cgi-bin/sendmsg.lua?cmd=SET+SLNT+0"
{"INFO":{"CMD":"SET SLNT","RSP":"OK"},"DATA":{"SLNT":0,"PWR":1,"F2L":0,"F2LF":0},"SUCCESS":true}%

Mac@Flobul % curl "http://192.168.XXX.XXX/cgi-bin/sendmsg.lua?cmd=SET+SLNT+1"
{"INFO":{"CMD":"SET SLNT 1","RSP":"TIMEOUT","MSG":"Stove communication failed"},"DATA":{"NODATA":true},"SUCCESS":false}%
```

Domochip, 2024-01-30:
Hi,

SET+SLNT+1 should not return a timeout error, this is effectively a bug.
Regarding SET+SLNT+0, it does nothing...

I'll have a look at this bug shortly.
thx

Domochip, 2024-02-04:
Hi, Could you give it a try with the latest pre-release?
If the error still occur, I'll need your GET+STDT to understand, what happens.

Flobul, 2024-02-04:
Hi.

```
Mac@Flobul % curl "http://192.168.23.49/cgi-bin/sendmsg.lua?cmd=SET+SLNT+0"
{"INFO":{"CMD":"SET SLNT","RSP":"OK"},"DATA":{"SLNT":0,"PWR":1,"F2L":0,"F2LF":0},"SUCCESS":true}%
Mac@Flobul % curl "http://192.168.23.49/cgi-bin/sendmsg.lua?cmd=SET+SLNT+1"
{"INFO":{"CMD":"SET SLNT 1","RSP":"TIMEOUT","MSG":"Stove communication failed"},"DATA":{"NODATA":true},"SUCCESS":false}%
```

Initial values : FAN OFF and POWER 1. When I send SLNT+1, POWER is set to 3. Nothing happens on SLNT+0.

Domochip, 2024-02-04:
Hi,

First, thank you, following the track, I found a bug I introduced recently (I just fixed the pre-release).
Regarding your issue, The "SILENT" mode seems to be designed for Stove which have FAN3 and FAN4 (additionnal Air ducts or Water pumps).

Here is what it is doing: Set RoomFan, FAN3 and FAN4 to 0
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
Your Stove has FAN2TYPE = 2 which means you have only Room Fan and then iSetRoomFan3Atech return an error.

So for your model, you just need to do a SET+RFAN+0
I will improve error messages of WPalaControl in next release, then it will return an UNSUPPORTED error.

Flobul, 2024-02-04:
You're welcome.

Only ROOM FAN on my stove, exactly.

I just tested your latest fix, same cmd results than before, but now POWER is no more set to 3 anymore.

Closed 2024-02-04.

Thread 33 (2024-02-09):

Add F3L and F4L setting

carmelo42, 2024-02-09:
Just tried the 2.1.5/3.1.2v2 pre-release :

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

It works great :)

I can change the main fan setting (F3L) but there are 2 settings missing : left and right fans (F3L and F4L) :

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

Domochip, 2024-02-09:
Thank you for the feedback.
I had a doubt about this part because my stove doesn't have this additionnal fans.
So, if I understand well, it would be better to have 2 sliders for F3 and F4, right? With value from 0 to 5?

carmelo42, 2024-02-09:
Yes exactly :)
2 sliders for the 2 additional fans, scale 0 to 5.

pm2036, 2024-02-09:
Hello,
On my stove, F3L and F4L is only 0/1. Maybe it depends of the stove model?

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

carmelo42, 2024-02-09:
Mine is "TURBOFONTE TAL" which is I think the same as PALAZZETTI JULIA :

```
// 20240209100452
// http://192.168.0.239/cgi-bin/sendmsg.lua?cmd=SET+FN4L+4

{
  "INFO": {
    "CMD": "SET FN4L",
    "RSP": "OK"
  },
  "DATA": {
    "F4L": 4
  },
  "SUCCESS": true
}
```
On the MQTT bus :
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

And for the other fan :
```
// 20240209100713
// http://192.168.0.239/cgi-bin/sendmsg.lua?cmd=SET+FN3L+4

{
  "INFO": {
    "CMD": "SET FN3L",
    "RSP": "OK"
  },
  "DATA": {
    "F3L": 4
  },
  "SUCCESS": true
}
```
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

pm2036, 2024-02-09:
Ok, mine is a Palazzetti Allegro

`http://192.168.110.70/cgi-bin/sendmsg.lua?cmd=SET+FN3L+4`
`{"INFO":{"RSP":"OK","CMD":"SET FN3L","TS":1707471245},"SUCCESS":true,"DATA":{"F3L":1}}`

I think the max value is in sendmsg.lua?cmd=GET+ALLS
"FANLMINMAX":[0,5,0,1,0,1]

Domochip, 2024-02-09:
Yes, FANLMINMAX contains these limits.
2 firsts numbers are min and max for RoomFan (aka FAN2)
2 nexts are for F3
then 2 last numbers are for F4

So, the good option id to use some switches for stove which have "0,1" limits and sliders for "0,5" limits
I'll implement that shortly

Domochip, 2024-02-09:
V3 prerelease is available and adjust the HomeAssistant Entity type based on the Fan Min and Max values.
Could you let me know if it fit your needs?

carmelo42, 2024-02-09:
It works great :)

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

Domochip, 2024-02-09:
In your case, switch buttons can be removed then

carmelo42, 2024-02-09:
Yes I will remove them.
I'm happy, I've removed https://github.com/marcopal74/home-assistant-palazzetti which was not working every time.

pm2036, 2024-02-09:
Ok for me too, thanks.
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

Closed 2024-02-18.

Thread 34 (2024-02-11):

SET+PWR+2 sent instead of SET+POWR+2

carmelo42, 2024-02-11:
Hello,

From HA, when is use the slider to set fire power to 2, the command sent is SET+PWR+2 instead of SET+POWR+2 so it doesn't change the value:

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

If I send the correct command through HTTP it's ok:
```
// 20240211090505
// http://192.168.0.239/cgi-bin/sendmsg.lua?cmd=SET+POWR+2

{
  "INFO": {
    "CMD": "SET POWR",
    "RSP": "OK"
  },
  "DATA": {
    "PWR": 2,
    "F2L": 2,
    "FANLMINMAX": [
      0,
      5,
      0,
      5,
      0,
      5
    ]
  },
  "SUCCESS": true
}
```

Domochip, 2024-02-11:
thx, I republished the v3 prerelease with to fixed topic

carmelo42, 2024-02-11:
Flashed, and it works fine :)
Thanks a lot :)

Closed 2024-02-11.

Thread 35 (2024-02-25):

Not working on ESP01

Christoffer-da, 2024-02-25:
I tried to flash and run on another esp8266 variant, the esp01.
Unfortunately it flashes well, but won't run.
I get the rst error 4, boot mode 3.7.

Would be nice to be able to use this firmware on the different esp8266 variants. This could also involve the possibility to set rx/tx gpio in the ui.

Christoffer-da, 2024-02-25:
When I get the time, I will try to change the board in platform io, and also the pin-out, to see if I can get everything working.

Domochip, 2024-02-25:
This project has been designed on D1 Mini which is much more convenient than ESP01. What is the benefit to run it on ESP01?

Christoffer-da, 2024-02-25:
For a project that basically only uses rx-tx, the small and cheap esp-01 might be better suited. You do not loose function, and it is way cheaper.
I mostly use the esp32, but for this it would be great to reuse a modbus module I have previously used to control my underfloor heating system.

For me the d1mini is great, and if I do not get it up and running, I might just buy from your tindie shop, for the ease of it.

Closed 2024-03-02.

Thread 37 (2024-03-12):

Add another rj11 connector on the board

Christoffer-da, 2024-03-12:
Just received the board, and now awaiting the last pieces, to be able to install.

I do not know if this is a valid suggestion, but here we go:

If you add another RJ11 connector on the next revision of the board, bridged with the existing one, the we could save one cable and the external rj11 splitter. It would also make your board, baught on Tindie, a drop in component, without the need to buy extra stuff elsewhere.
It woul be nice to just put this board in between the existing connection on the stove controller.

Flobul, 2024-03-27:
Some stoves have a spare RJ11 connector on the back of it.
I wonder, what is the rate of stoves without/with spare RJ11 on the back ?

I think, adding a RJ11 to the board would make it bigger and the board would not fit the size of the ESP8266 Wemos anymore.

Domochip, 2024-09-04:
I agree with @Flobul, there is not so much stove without the rj11 on the back.
Anyway, I documented the Y adapter required and also, I have some in stock too.

Closed 2024-09-04.

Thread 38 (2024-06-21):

MQTT fail after power outage

SlackPhoby, 2024-06-21:
Hi,
Thank you for this great work! Sorry for my English.
I am reporting a bug that occurs after a power outage. The MQTT connection is lost, and 4 out of 6 chips on the same network fail to reconnect. The other 2 chips reconnect successfully. The failing chips require a manual restart to function again.
I have 5 of them connected to the OpenHab MQTT broker. Three of them fail after a power outage, and 1 connected to Home Assistant fails too.
The problem started after upgrading the firmware to 2.1.4. Before that, I was using version 1.4.1, and it worked well.
Thanks again for your work.
Sincerely,
Axel
I hope this is helpful!

Domochip, 2024-06-24:
Hi,
Thanks for your feeback.
Could you let me know which exact version is currently on your module?

Domochip, 2024-06-24:
ok,

For confirmation, you have 5 WPalaControl (and so 5 stoves) on the same Wifi network?
When you got the issue, modules were reconnected to the Wifi and only the MQTT was disconnected?
Did you got any other issue or instability?
Could you let me know what is your MQTT configuration in one of your WPalaControl module?
Does all module are configured the same way?

thanks

SlackPhoby, 2024-06-24:
Hi,
Yes, I have 6 stoves, each with its own wirelespalacontrol device, all on the same network (it's a tourist complex with cabins). I have a single Raspberry Pi with openHAB functioning as an MQTT broker. After a power outage, all of them connect well to the WiFi, but not all connect to the MQTT. All the devices have the same configuration. I think the problem is that the WiFi network comes up faster than the Raspberry Pi with openHAB starts, so they try to connect to an MQTT broker that hasn't started yet, but then they don't try again; they simply remain disconnected. For them to connect, I have to do a manual restart, and then they connect fine.

The strange thing is that before updating the version, it worked well, so I don't think it's a network or device configuration issue since the only thing I changed was updating the firmware. The configuration is exactly the same as it was with version 1.4.1.

Once connected, the devices work perfectly, with no instability or any other issues.

The MQTT configuration is as follows:

Type: MQTT
Upload period: 60
Hostname: [ipbroker]
Port: [1883]
No username
No password
Base topic: $model$
MQTT type: generic

Domochip, 2024-06-30:
Hi,
Sadly, I was not able to repeat the problem on my side.
But I can see only one place where the problem can occur in the code.
In my MQTT Management library, if the MQTT client is not connected, it will always retry to connect, except if a disconnection has been called.
https://github.com/Domochip/WirelessPalaControl/blob/04ef6ba220e5e0dfc10867c8054c544e4dda59ee/src/base/MQTTMan.cpp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

WPalaControl do not disconnect MQTT except during a reboot but if MQTT is configured, a connection is executed just after.
This means that PubSubClient (underlying library to connect to MQTT) should never return a state equals to MQTT_DISCONNECTED.

BUT there is a specific case which switch the state to MQTT_DISCONNECTED even if I don't call disconnection method, here :
https://github.com/knolleary/pubsubclient/blob/2d228f2f862a95846c65a8518c79f48dfc8f188c/src/PubSubClient.cpp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

and then, I can find this issue which is mentionning this code :
https://github.com/knolleary/pubsubclient/issues/927

I so have some new questions for you 😉 :
- what broker are you using and which version of it?
- did you got the problem only during a power outage
- did the problem occured multiple time (did you got multiple outage?)

thanks for your help

SlackPhoby, 2024-07-01:
Hi, yes of course, whatever you need!
Currently, I have 5 stoves connected to Mosquitto MQTT v3 installed on a Raspberry Pi with OpenHAB 3.4. Out of these 5, 3 always fail (I live in a mountainous area with frequent snowfalls, so I have frequent power outages).
The other stove is connected to Mosquitto MQTT v5 (latest version) installed on a Beelink mini PC with Home Assistant (also latest version), and it always fails after a power outage.

The failures occur **only** after a power outage. After a manual restart, they connect perfectly and do not fail. They work perfectly, with no connection errors or command loss, until the next power outage, when they fail again.

Attached is a photo of how the main tab looks after a power outage and another one after restarting and working properly.
After power outage:
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
After reboot, working:
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

Domochip, 2024-09-04:
Hello,
Ok, you are using Mosquitto as Broker but the version number you gave is not the Mosquitto version.
For example, the latest on is 2.0.18 (https://mosquitto.org/download/)
Could you check the version?

SlackPhoby, 2024-09-05:
Hi, yes
On a Raspberry Pi with OpenHAB 3.4

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

On a Beelink mini PC with Home Assistant

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

These are the versions I am currently using and in which this issue persists. thanks

Domochip, 2024-09-05:
ok, I'll try to simulate wifi disconnection with a metal box and I can control an MQTT broker myself

Domochip, 2024-09-07:
Thanks a lot for your patience, I was able to debug it and found the issue.
The latest release fix the problem.

Closed 2024-09-08.

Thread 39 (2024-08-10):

No stove connection during initialization byte 0x201c in iGetStatusAtech function

dxmen7, 2024-08-10:
Hello, I have following issue, I have debugged every single line until Palazzetti.cpp line 1013:
Palazzetti::CommandResult Palazzetti::iGetStatusAtech()
{
    CommandResult cmdRes;
    // die zeile gibt nicht erwarteten wert zurück
    cmdRes = fumisComReadByte(0x201C, &_STATUS);
    if (cmdRes != CommandResult::OK) {
        Serial1.println("fumisComReadByte(0x201C, &_STATUS) != CommandResult::OK");
        return cmdRes;
    }

Here the controller tries to read byte =x201c and expects specifc byte value, but this failed. Without knowledge about Fumis byte structure it's difficult for me to go ahead.
DO you have an idea or more background knowledge about Fumis byte structure?

I have a Fumis Alpha UI from JOTUL stove connected to Fumis controller, where I connected my RJ11 cable to my controller.
If you need further information, please let me know.

Debugged serial Rx/Tx on stove and µC side looks fine.

Domochip, 2024-08-30:
Hello,

What is your motherboard model?

Domochip, 2024-09-04:
I can only imagine 2 scenario :
 - there is a problem with the adapter and/or cable
 - your  motherboard is not compatible

Could you give me more details about your motherboard and explain how you cabled it?

dxmen7, 2024-09-04:
Hello,Thanks for your reply. Yes I will give you my motherboard model number this weekend, I have to partially dismount my stove. I checked the adapter several times with a friend together and measured every single element. In my opinion, there can be a risk with a newer hardware version from Fumis and potentially an incompatibility. On 4. Sep 2024, at 20:52, Domochip ***@***.***> wrote:
I can only imagine 2 scenario :

there is a problem with the adapter and/or cable
your  motherboard is not compatible

Could you give me more details about your motherboard and explain how you cabled it?

—Reply to this email directly, view it on GitHub, or unsubscribe.You are receiving this because you authored the thread.Message ID: ***@***.***>

dxmen7, 2024-09-04:
Sorry,Forgot the second part. Cabled it by RJ11 cable and modified as you described in your repo with crossing the lines.This cable goes to adapter, adapter is on top of D1 Mini and d1 mini Ports also correct.With serial monitor I have checked Rx and Tx on both sides and can see an Tx by D1 Mini after receiving an Rx and vice versa from stove side. On 4. Sep 2024, at 20:52, Domochip ***@***.***> wrote:
I can only imagine 2 scenario :

there is a problem with the adapter and/or cable
your  motherboard is not compatible

Could you give me more details about your motherboard and explain how you cabled it?

—Reply to this email directly, view it on GitHub, or unsubscribe.You are receiving this because you authored the thread.Message ID: ***@***.***>

Domochip, 2024-09-05:
ok, in that case I advise to take some pictures too at the same time you open it ;-)

dxmen7, 2024-09-08:
Hello from Germany,

I was not able to open side panel for direct access to motherboard.
I only have model type, vendor serial number under device model of UI panel at the side of the stove.
Maybe this help you too.
Attached pictures how is the controller cabled to stove.
I will try gonget more information and manual, how to open side panel.

Please find here iCloud Link to pictures, attaching to mail is too big: https://share.icloud.com/photos/012Ni27n0eGaETrfiNwn6vIIw

Best,
Dennis

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

Domochip, 2024-09-08:
Hello,

When you plug the stove to the module without powering the d1mini, do you see the D1 diode blinking (activity of the stove bus)?
does an error appears on the stove screen after 10sec?
Same questions but with the d1mini powered?

dxmen7, 2024-09-08:
Hello,
Yes, LED on stove side is blinking and confirmed with bus analyzer, that Tx and Rx are transmitted and received frames.
D1 mini powered also.
NO error on stove side after 10 sec.

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

Domochip, 2024-09-08:
What's your Jotul stove model? Do you know if Jotul offers a "ConnectionBox" or a module to control it via mobile phone?

dxmen7, 2024-09-08:
It’s Model PF733 from Jotul.
Yes they offer a WiFi connection box with mobile app for one 200€, that was my trigger to try it by myself with your repo.

Service man also have a RJ11 cable with him to control stove via proprietary software provided by Jotul.
Connection box link with Jotul App you can find here: https://intl.jotul.com/sites/importers/files/products/JOTUL_PELLET_CONTROL_Manual_EN.pdf

Stove manual here: https://www.jotul.de/sites/deutsch/files/products/DE%20%20PF733-%20PNMU00049.pdf

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

Domochip, 2024-09-08:
OK, it should definitely be compatible with my module.

few seconds after powering the d1mini, you should see D3 led blinking shortly. Is that the case?

What's appears in the web page?

dxmen7, 2024-09-08:
Yes, D3 LED is blinking shortly after powering up.
Web Page looks like this:
￼
Uptime currently less than 1 min. But also after 5 mins same behavior.

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

Domochip, 2024-09-08:
The webpage image does not appears. could you paste it in github page directly pls
Which firmware are you using?

dxmen7, 2024-09-08:
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
 I am using firmware 2.1.5/3.1.2

Domochip, 2024-09-08:
OK, log is going out of D4 pin at 38400bps
First you can have look at what's logged.

Do you know how to create a platformio/arduinoIDE project and compile it?
if yes, I advidse you to use this very basic example : https://github.com/Domochip/Palazzetti/blob/master/examples/Serial_esp8266/Serial_esp8266.ino
if No, I can compile it for you

dxmen7, 2024-09-08:
Yes I have compiled it with Arduino IDE, but don't get any useful output. tried different Baudrates for serial monitor

Domochip, 2024-09-08:
What output do you get?

Domochip, 2024-09-08:
baudrate is 38400bps

Domochip, 2024-09-08:
the log is coming out of the D4 pin.
you need an additionnal serial adapter connected to GND and D4 to receive the log

dxmen7, 2024-09-08:
yeah was my fault, I will get one and come back to you

Domochip, 2024-09-08:
no problem ;-)

dxmen7, 2024-09-08:
Got it, unfortunately everything failed :(

wSer started
initialize Failed
myPala.getSetPoint failed
myPala.getAllTemps failed
myPala.GetStatus failed

Domochip, 2024-09-08:
do you have a logic analyzer?

dxmen7, 2024-09-08:
A friend of mine yes. What do you need for information?

Domochip, 2024-09-08:
The goal is to monitor exchanges on tx AND rx of the d1mini with real timing.
That's the ultimate solution to debug what's happening.

Another idea would be to log serial from micro-usb port + another adapter on D7.
But it needs to log the precise timing to be able to reconstruct the "discussion"

Domochip, 2024-09-11:
Hello, could you also try to remove R8 resistor or D3 led?

Domochip, 2024-09-11:
also what's your si8621 exact model (2 letters after 8621)?

dxmen7, 2024-09-11:
I have SI8621EC chip. Asked you former time as I ordered these.
One additional hint, I am using white LEDs, tried red ones earlier, but then D1 Mini didn‘t Boot with Adapter because of too high current flow through LED, with white one and slight higher voltage drop, adapter boots fine.

Domochip, 2024-09-12:
thx, I looking for increasing the R8 value to 2Kohms instead of 1K (maybe more will be needed)
Another person reported it in issue #42

dxmen7, 2024-09-14:
Desoldered R8, nothing changes, what do you need exactly for Rx/Tx or what should I try?

dxmen7, 2024-09-14:
I did it and can provide a picture: D0 is RX, D2 is TX. After Reset of D1 mini, Snapshot was created from UART Decoder
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

dxmen7, 2024-09-14:
can also provide PulseView file:
[dxmen7_domo_snapshot_rx_tx_pulseview.zip](https://github.com/user-attachments/files/17002379/dxmen7_domo_snapshot_rx_tx_pulseview.zip)

Domochip, 2024-09-14:
ok, this is exactly what I needed (pulseview file). I will compare it with mine shortly.
First look shows correct behavior but I need to check the answer of the stove.
when stove send a frame starting by 0x00, board can send a frame starting by 0x02 to read data. Stove immediately reply with a frame starting by 0x02 containing the answer

Domochip, 2024-09-18:
Hello, I just had mine connected and compared traces.
Yours:
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
Mine:
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

So, I can tell that you need to check this part:
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
Normally, when uC send something, it should be received back and in you case, nothing come back.

dxmen7, 2024-09-18:
Thanks for explanation! I have an idea.

where does Pin 6 on controller side at RJ12 connector get the power of stove side in your description?
I see in my setup a big mistake, I have a RJ11 cable with RJ11 connector. Thought it was a RJ12 one with 6 wires.

so in theory base of transistor Q1 don‘t get any power to connect.

did you use normal phone cable RJ12 or RJ12 cross over or do it by yourself by cutting and soldering the lines one by one?

Domochip, 2024-09-18:
sorry, I didn't exactly understand what you mean.
As described here : https://github.com/Domochip/WirelessPalaControl#connect
I'm using an RJ11 cable (4 wires) and they are crossed (don't seems to be common in the end)

dxmen7, 2024-09-18:
Okay understood. I have also a RJ11 cable and crossed the wires by myself because didn‘t get online a cross over cable.
with only 4 wires, I don‘t understand, how base of Q2 is powered of Pin 6 by J1?
In your picture, it looks like that out of J1 you have 5 lines, but only 4 are connected to the stove.
when Q2 isn‘t switched up, I think there is the communication problem on my side at the uC.

dxmen7, 2024-09-18:
Ah, now got it.

Domochip, 2024-09-18:
Base of Q2 is powered by R5 or not powered when Q1 is ON
Pin 6 is not used and I don't know its real usage but there was a switch on my original CBox, so I've made this solder jumper for the future if we discover something new.

szengerle, 2024-09-21:
Supported @dxmen7 on hardware level - TL;DR: Q2 was the root-cause
With the knowledge that signal must be looped back to MCU / MCU TX must be on TxRx put the SuT into some test circuit:
- TxRx to high (1MΩ)
- Square TX signal from MCU (signal generator)
- VCC/GND on both sides

Results:
- Q1 is working - feeding square into Q2's base
- Q2's collector is high - no square; 0/5V square on base

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

- 5V Emitter to VCC voltage

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

Replaced Q2:
- Voltage is droping now on base - square also on collector
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

- MCU side Rx shows also looped-back signal
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

@dxmen7 will test later with controller connected

dxmen7, 2024-09-21:
Now communication with stove works, as you said, after 10sec appears communication error on Stove screen with error code E004, is this the correct behaviour?

dxmen7, 2024-09-22:
Solved the last issue, cable was interrupted... now it works!
Thank you so much for your support! How can I donate your work?

Domochip, 2024-09-22:
Cool that it works now 👍
I have a paypal at domochip@hotmail.com

Domochip, 2024-09-22:
Thank you so much for your donation!
This helps me a lot for my home automation and electronics projects.
👍

Closed 2024-09-22.

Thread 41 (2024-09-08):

Stove communication failed

1300371, 2024-09-08:
I use WPalaControl since 3 years now without issues.

Usually, i unplugged (from electric power) the stove and WPala module from winter to automn.
I replugged recently my setup and saw that WPalaControl failed to communicate with stove.

My tries until then:
- check/switch cable
- update firmware from 1.4.1 to 2.2.2

When i plugged the stove to the module, some LED lights up but WPalaControl indicates:
`MSG : Stove communication failed! please check cabling to your stove.`

I changed nothing from last usage...

Is there a way to check logs from WPalaControl ? It's like the module can communicate with stove but info from stove are kind of wrong.

Domochip, 2024-09-08:
If you connect the module to the stove without powering it (micro-usb disconnected), do you see the D1 led blinking (next to the RJ11 connector)?

1300371, 2024-09-08:
Yes

Domochip, 2024-09-08:
The log is going out to the pin D4 on d1_mini. That means you need to solder a cable to a separate serial adapter.

Domochip, 2024-09-08:
otherwise, if you have an ESP32 miniKit like this :
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
Then you can get the log directly to the usb serial of the module

1300371, 2024-09-08:
I use this

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

Domochip, 2024-09-08:
I advise you to check soldering of U1 maybe for a bad contact.
It is usually the difficult point where I'm finally cheking with microscope

1300371, 2024-09-08:
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

Maybe the issue ... Will try to resolder 🤞

1300371, 2024-09-08:
Tricky to sold ... but i was that !!
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
Thank you so much ❤️

Domochip, 2024-09-08:
yw 😉

Closed 2024-09-08.

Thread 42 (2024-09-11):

ESP not booting with Adapter attached

Padm59, 2024-09-11:
When the adapter is connected with the Wemos D1 Mini, it will not boot because pin D8 is pulled high through R8 and LED3.

As described in the Pinout below -> Best Pins to use - ESP8266:
https://randomnerdtutorials.com/esp8266-pinout-reference-gpios/

Quick Fix:
Just desolder R8 and it works.

Domochip, 2024-09-11:
Are you using a RED led too?

Padm59, 2024-09-11:
yes👍

Domochip, 2024-09-11:
what's your si8621 exact model? (two letters after 8621)

Padm59, 2024-09-11:
I have the si8621EC and besides of the following the exact same components.
I still have another connection problem besides the boot problem. This could be my fault though because I used another diode and not the SS34. Mine has a slightly higher forward voltage drop and is probably a bit slower switching.
I do get values and I have control half of the time. It loses the connection every other minute or so. When it looses the connection it only shows an empty serial number.

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

Domochip, 2024-09-22:
Hey,
Did you made some progress? Do you need help?

Padm59, 2024-09-27:
Going to look into it again this weekend, maybe I get my pi pico to work as a logic analyzer.

Padm59, 2024-09-27:
I used the same red LED on the VDD input of the stove, maybe it just has a to high of a voltage drop to work correctly. When connected with the stove, the LED is also flickering all the time. For the power, I guess this could be the problem?
Also doing some sampling of rx and tx on the esp side. Will take a look at them later in detail.

I could try to just remove the LED D1 so that the level shifter and pullups have a higher voltage. tx and rx on the stove side is 5V so why should they be only pulled to roughly 3V or so.

Padm59, 2024-09-27:
[betweenR2andlevelshifter_txstove.zip](https://github.com/user-attachments/files/17169056/betweenR2andlevelshifter_txstove.zip)
[txrxesp_onpagerefresh_stoveconnected_withdata.zip](https://github.com/user-attachments/files/17169057/txrxesp_onpagerefresh_stoveconnected_withdata.zip)

This was recorded the moment after I refresh the webpage and I triggered of the tx channel. I had connection to the stove and also got data back in the web interface after the refresh. Maybe it helps, baudrate was 38400 right?
Also the tx line on the stove side looks really messy, probably because of the very destorted and low VDD line.

Domochip, 2024-09-27:
2 things:
- regarding the schematic, I just reproduced the original one I had, so I don't know why it is powered this way (but is working fine)
- did you changed your diode to a proper SS34?

Padm59, 2024-09-27:
I still have the other diode on the board, but I bridged the LED, and now it's working perfectly fine so far.
I had a glance at the signal, and it looked much better without all the noise.
https://mm.digikey.com/Volume0/opasdata/d220001/medias/docus/3694/B1911USD-20D000114U1930.pdf
That's the red led I removed. So I have no led on the board at the moment.
Doing a longer test tonight to see if there are still any communication errors. We will see tomorrow.

Domochip, 2024-09-28:
I'm using any red led found on aliexpress. I can only advise you to use an SS34 as specified in the schematic...

Padm59, 2024-10-02:
Got my self a SS34 yesterday, and now it works flawlessly. I did put the Red Led on VCC back and also have no noise anymore.
Now we know for sure that you won't get away with just unsing another diode😬
Thank you for your help and advise on this one

Back to the original reason why I opend this issue:

When either the LED3 or R8 are removed, it works. I don't need the led anyways.
Maybe use for R8 2kOhms or higher this could also work.

Closed 2024-10-02.

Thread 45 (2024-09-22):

Découvert impossible dans Home Assistant

Archange2222, 2024-09-22:
Bonjour

J'ai correctement configuré l'ESP et la connexion avec Home Status est OK

> Home Automation Status
> MQTT Connection State : Connected
> Last Publish Result : OK

Cependant Home Assistant ne le détecte pas automatiquement :

Mosquitto broker : 6.4.1
Home Assistant :
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

Merci

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

Domochip, 2024-09-22:
Bonjour,

Pourriez-vous me confirmer que le numéro de série du Poêle apparait sur la page de status (même si ce ne sont que des 0 pour Jotul):
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

Il faut ensuite utiliser "MQTT Explorer" et jeter un œil à ces topics (sont-ils présents):
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

Bonne Soirée

Archange2222, 2024-09-22:
Bonsoir

Le numero de serie apparaît bien

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

Dans MQTT explorer j'ai cela :

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

Domochip, 2024-09-23:
Bonjour,

Dans MQTT Explorer, c'est la partie dans **homeassistant** qui m'intéresse

Domochip, 2024-09-24:
Bonsoir,

Votre problème est-il résolu? Sinon, pourriez-vous me transmettre une capture de la partie **homeassistant** dans MQTT Explorer comme sur ma capture :
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

Archange2222, 2024-09-24:
Bonsoir,

pardon, voilà le bon imprim écran

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

Domochip, 2024-09-24:
ok, le module envoie donc correctement les infos à homeassistant.
Est-ce que les appareils sont bien apparus dans Home Assistant comme ceci (WPalaControl et Stove) :
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

Archange2222, 2024-09-25:
Bonjour

c’est bon il apparaît bien correctement, j’étais persuadé qu’il fallait faire un ajout manuel comme un nouvel appareil. Mais c’est bon il remonte bien et j’ai bien toutes les informations.

Merci pour votre aide et bonne journée

Closed 2024-09-25.

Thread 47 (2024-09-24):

Ventilation arrière

ec0li82, 2024-09-24:
Bonjour
Je viens de recevoir mon module, cela fonctionne, merci.
Sur mon poele (Palazetti Julie), j'ai une sortie arrière pour chauffer une pièce annexe.

J'ai une entité "left fan" qui a été détectée mais ne fonctionne pas (rien ne se passe, enfin si, le log book montre une déconnexion!).
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

J'ai remarqué que mon ventilateur arrière correspond à F4L :

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

Comment faire utiliser cette valeur dans home assistant?

Merci.

Domochip, 2024-09-24:
Bonjour,

Pourriez-vous m'indiquer le modèle de poêle que vous possédez?
Afin de comprendre cette inversion, pourriez-vous me transmettre les résultats des 2 pages web suivantes:
http://wpalacontrol.local/cgi-bin/sendmsg.lua?cmd=GET+STDT
http://wpalacontrol.local/cgi-bin/sendmsg.lua?cmd=GET+ALLS

Merci

ec0li82, 2024-09-24:
Les voici
{"INFO":{"CMD":"GET STDT","RSP":"OK"},"DATA":{"LABEL":"WirelessPalaControl","GWDEVICE":"wlan0","MAC":"34:94:54:8E:28:F3","GATEWAY":"192.168.0.1","DNS":["192.168.0.1"],"WMAC":"34:94:54:8E:28:F3","WMODE":"sta","WADR":"192.168.0.25","WGW":"192.168.0.1","WENC":"psk2","WPWR":"-59 dBm","WSSID":"BLAISE","WPR":"dhcp","WMSK":"255.255.255.0","WBCST":"192.168.0.255","WCH":"11","EPR":"dhcp","EGW":"0.0.0.0","EMSK":"0.0.0.0","EADR":"0.0.0.0","EMAC":"34:94:54:8E:28:F3","ECBL":"down","EBCST":"","APLCONN":1,"ICONN":0,"CBTYPE":"miniembplug","sendmsg":"2.1.2 2018-03-28 10:19:09","plzbridge":"2.2.1 2022-10-24 11:13:21","SYSTEM":"2.5.3 2021-10-08 10:30:20 (657c8cf)","CLOUD_ENABLED":true,"SN":"000000000000000000000000000","SNCHK":0,"MBTYPE":0,"MOD":397,"VER":43,"CORE":130,"FWDATE":"2016-04-18","FLUID":0,"SPLMIN":6,"SPLMAX":51,"UICONFIG":2,"HWTYPE":6,"DSPTYPE":1,"DSPFWVER":29,"CONFIG":2,"PELLETTYPE":2,"PSENSTYPE":0,"PSENSLMAX":0,"PSENSLTSH":0,"PSENSLMIN":0,"MAINTPROBE":4,"STOVETYPE":1,"FAN2TYPE":3,"FAN2MODE":3,"BLEMBMODE":3,"BLEDSPMODE":1,"CHRONOTYPE":0,"AUTONOMYTYPE":1,"NOMINALPWR":9},"SUCCESS":true}

{"INFO":{"CMD":"GET ALLS","RSP":"OK"},"DATA":{"MBTYPE":0,"MAC":"34:94:54:8E:28:F3","MOD":397,"VER":43,"CORE":130,"FWDATE":"2016-04-18","APLTS":"2000-04-07 11:56:13","APLWDAY":7,"CHRSTATUS":0,"STATUS":0,"LSTATUS":0,"SETP":0.00,"PUMP":0,"PQT":12147,"F1V":0,"F1RPM":0,"F2L":2,"F2LF":0,"FANLMINMAX":[0,5,0,5,0,5],"F2V":0,"F3L":0,"F4L":3,"PWR":1,"FDR":0.00,"DPT":0,"DP":67,"IN":13,"OUT":0,"T1":0.00,"T2":20.70,"T3":24.00,"T4":0.00,"T5":20.10,"EFLAGS":0},"SUCCESS":true}

Merci.

Domochip, 2024-09-24:
Bonsoir,

Je viens de faire l'ajustement sur la branche master.
Je vous propose d'essayer cette version du firmware qui doit résoudre votre problème.
[v2.2.2-3.1.5.rc.zip](https://github.com/user-attachments/files/17121453/v2.2.2-3.1.5.rc.zip)

Bonne Soirée

ec0li82, 2024-09-25:
Merci beaucoup ça fonctionne!
J'ai désormais également le setpoint. Celui ci reste a l'état inconnu. Peut être est ce normal si le poêle est éteint ?
Un get fonctionne:
{"INFO":{"CMD":"GET SETP","RSP":"OK"},"DATA":{"SETP":23.00},"SUCCESS":true}

Domochip, 2024-09-25:
Pourriez-vous me donner le contenu de ces topics avec "MQTT Explorer" :
WPalaControl/connected
homeassistant/number/WPalaControl_LT201XXXX_SETP/config
WPalaControl/SETP (attendre 1 minute max pour qu'il arrive)

ec0li82, 2024-09-25:
Bonjour, les voici.
Screenshot pour le 1er et le 3e:

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

Valeur pour le second :

`{"~":"WPalaControl","availability":{"topic":"~/connected","value_template":"{{ iif(int(value) > 0, 'online', 'offline') }}"},"command_template":"SET+SETP+{{ value }}","command_topic":"~/cmd","device":{"configuration_url":"http://wpalacontrol.local","identifiers":["WPalaControl_000000000000000000000000000"],"model":"397","name":"Stove","sw_version":"43 (2016-04-18)","via_device":"WPalaControl_3494548E28F3"},"device_class":"temperature","min":17,"max":23,"mode":"slider","name":"SetPoint","object_id":"stove_setp","state_topic":"~/SET","unique_id":"WPalaControl_000000000000000000000000000_SETP","unit_of_measurement":"°C","value_template":"{{ value_json.SETP }}"}`

Bizarre que je n'ai pas de numéro de serie LT alors que c'est un Palazzeti (après avoir lu d'autres issues, ca devrait etre le cas)?
Mon installateur n'a jamais su me donner de numéro de série quand je lui ai demandé, car Palazetti m'en demandait pour remplacer ma cbox HS.
Je n'ai aucune plaque ni aucun numéro inscrit à l'arrière...

Domochip, 2024-09-25:
ok, coté MQTT, tout est correct. L'entité SetPoint devrait être disponible. Je conseille juste un reboot du WPalaControl pour que ce soit repoussé. Si ça ne fonctionne toujours pas après, il faudra donc que l'on regarde coté HomeAssistant.

Très étrange oui pour le numéro de série. Ce sont bien des 0 pour les Jotul mais pour les poêles Palazzetti, il est sensé être programmé et étiqueté sur le poêle...

ec0li82, 2024-09-25:
OK. j'ai rebooté le wpalacontrol mais meme chose.
En fait l'entité est bien là mais la valeur n'est pas rapportée.
Par exemple via wpalacontrol je vois bien le setp actuellement à 21 (valeur egalement sur le poele)
Par  contre HA lui n'a pas de valeur.
Sur la page web, le slider est au milieu (20 quand je passe avec la souris comme ici) :
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

En cliquant pour voir les details/l'historique, il ne recoit en fait aucune valeur
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

Si je met une valeur en utilisant le slider, le setp est bien appliqué dans wpala et constaté sur le poele. Cependant HA ne l'affiche toujours pas et le slider revient au centre après un refresh.
Si je change la temperature sur le poele, meme chose : le setp est bien recu sur wpala mais pas dans HA.

Je precise que le poele est sous tension mais pas actif, c'est peut etre normal tant qu'il n'est pas "allumé" ?

Domochip, 2024-09-25:
Merci beaucoup pour ces retours précis.
La consigne (aka setPoint) doit remonter même si le poêle est sur OFF.
Vos retours m'ont permis de trouver une erreur dans le code pour la découverte Home Assistant.
Voici donc la version corrigée :
[v2.2.2-3.1.5.rc2.zip](https://github.com/user-attachments/files/17130229/v2.2.2-3.1.5.rc2.zip)

ec0li82, 2024-09-25:
C'est parfait avec cette nouvelle version !
Merci beaucoup !

Domochip, 2024-09-25:
Elle corrige ce problème, mais je viens d'en remarquer d'autres.
La valeur ne se met pas à jour immédiatement.
Je vais améliorer le fonctionnement avec ce mode de publication MQTT

Domochip, 2024-09-28:
Je viens de de faire une pré-release qui améliore tout cela du coup : https://github.com/Domochip/WirelessPalaControl/releases/tag/v2.3.1-3.1.5

ec0li82, 2024-09-28:
Effectivement c'est beaucoup plus réactif !
Merci!

Domochip, 2024-09-28:
;-) de rien

Closed 2024-09-28.

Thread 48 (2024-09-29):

Failure to build related to ArduinoJson - regression

sven337, 2024-09-29:
Hi,
I am unable to build due to the following error:
```
src/base/Application.cpp: In member function 'bool Application::loadConfig()':
src/base/Application.cpp:105:18: error: 'ArduinoJson::V6214PB2::JsonDocument::JsonDocument()' is protected within this context
  105 |     JsonDocument jsonDoc;
      |                  ^~~~~~~
In file included from .pio/libdeps/d1_mini/ArduinoJson/src/ArduinoJson/Document/BasicJsonDocument.hpp:7,
                 from .pio/libdeps/d1_mini/ArduinoJson/src/ArduinoJson/Document/DynamicJsonDocument.hpp:7,
                 from .pio/libdeps/d1_mini/ArduinoJson/src/ArduinoJson.hpp:33,
                 from .pio/libdeps/d1_mini/ArduinoJson/src/ArduinoJson.h:9,
                 from src/base/Application.h:14,
                 from src/base/Application.cpp:1:
.pio/libdeps/d1_mini/ArduinoJson/src/ArduinoJson/Document/JsonDocument.hpp:280:3: note: declared protected here
  280 |   JsonDocument() : pool_(0, 0) {}
      |   ^~~~~~~~~~~~
```

This is a regression introduced by that commit:
```
commit 5165ec0d679e07a6e79a5fa38757287f62cfbb04
Author: DomoChip <domochip@hotmail.com>
Date:   Sat Feb 3 15:03:48 2024 +0100

    Update WirelessBase to 2.1.5

 src/base/Application.cpp | 42 ++++++++++++++----------------------------
 src/base/Application.h   |  2 +-
 src/base/Core.cpp        |  2 +-
 src/base/Core.h          |  2 +-
 src/base/Version.h       |  2 +-
 src/base/WifiMan.cpp     |  2 +-
 src/base/WifiMan.h       |  2 +-
 7 files changed, 20 insertions(+), 34 deletions(-)
```

sven337, 2024-09-29:
My apologies: I have little experience with platformio and did not know I was supposed to "platformio pkg update" first.
This builds fine with an up-to-date ArduinoJson.

Domochip, 2024-09-29:
yes, I'm looking to define the minimum version of ArduinoJson in platformio.ini file

Closed 2024-09-29.

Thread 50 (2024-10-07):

Not responsive after some time

ec0li82, 2024-10-07:
Hello
For the second time, my WirelessPalaControl became unresponsive. This time it's after 4 days. Latest firmware.
Not available/disconnected in ha
Web gui not responding
IP not pinging
RJ11 led stays red as normal
Only solution is replug USB power.

I'm wondering if it's DHCP (ip set in DHCP server)...I've set a static IP directly now...let's see.
Wondering about my USB power source, will change that next time...
How to troubleshoot further?
Thanks.

Domochip, 2024-10-08:
If there is no wifi connection, the module switch automatically to AccessPoint mode.
An interesting thing would be to go close to the module and see if the Wifi network named "WirelessPalaControlXXX" appears

ec0li82, 2024-10-08:
Happened again after 12 hours.
Was not in ap mode.
I've now changed the USB plug and cable. Let's see

ec0li82, 2024-10-14:
Seems stable now... Let's close

Closed 2024-10-14.

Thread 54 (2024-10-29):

Stove communication failed

Palyndiel, 2024-10-29:
Bonjour,

Je n’arrive plus à faire fonctionner le module palacontrol avec mon poêle Turbo Fonte.
Le boîtier fonctionnait encore en début d’année mais en le rebranchant en début de mois, impossible de le faire fonctionner.
J’ai le message d’erreur suivant :
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

Version du module :
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

La petite led rouge est bien allumée :
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

Merci de votre aide.

Domochip, 2024-10-29:
Je vous conseille de contacter le vendeur de votre module dans ce cas

Domochip, 2024-11-01:
Bonsoir,
Avez-vous eu un retour de votre vendeur?

arabine, 2024-11-02:
Bonjour, j'ai exactement le même problème avec un module que je viens d'acheter sur TIndie. Normalement j'ai le bon modèle de poële...

Domochip, 2024-11-02:
@arabine
L'avez-vous acheté auprès de moi?
Si tel est le cas, pourriez-vous plutôt me contacter via Tindie. Je pense que c'est une meilleure option pour suivre le SAV

Bonne Journée

Domochip, 2024-11-02:
Petite clarification:
- Je ne sais pas qui est DIYPala (autre vendeur sur Tindie)
- J'ai ouvert ma boutique Tindie il y a un peu plus d'un mois sous mon pseudo Domochip
- Auparavant, les gens me contactaient par mail et je vendais en direct.
- @Palyndiel : je n'ai jamais fabriqué de PCB blanc. Je n'en suis donc pas le fabricant...
- @arabine : votre nom n'apparait pas dans ma liste de commande. Je ne pense donc pas en être le fabricant non plus.

Malgré tout, le but de ce projet est d'aider les gens à améliorer leur habitat.
Je n'ai pas de soucis à aider tout utilisateur mais pour des problèmes matériels comme les vôtres, il n'y a que 2 options:
- je suis le fabricant : j'assure le SAV
- je ne suis pas le fabricant : c'est à vous de chercher la panne avec mon aide

Si vous n'avez pas de retour de vos fabricant et que vous souhaiter résoudre le problème, n'hésitez pas à donner un maximum de détails (marque et modèle du poêle, année d'achat du WPalaControl, version actuelle du firmware, votre poêle a-t-il une prise accessible ou bien un splitter a dû être ajouté, etc, ...)

@arabine si vous entrez dans ce dernier cas, Il faudra plutôt que vous ouvriez votre propre issue

Bonne Journée

arabine, 2024-11-02:
@Domochip oui mon vendeur est bien DIYPala, je suis entré en contact avec lui il m'a répondu, c'est donc en cours. Si on ne parvient pas à trouver le problème j'ouvre un ticket ici, de tout tracer peut aider les prochaines personnes ayant le même soucis.

(j'ai du matos électronique et je code du firmware donc je peux aider).

Merci !!

Palyndiel, 2024-11-02:
Bonjour, petit retour de mon côté. Après avoir passé 1h à faire du debug dans platformio, et après plusieurs nettoyage/reecriture, le module est tombé en marche.
Donc le matériel fonctionne effectivement mais je pense qu’il y a bien un problème software.

Domochip, 2024-11-02:
Bonjour,
Avez-vous flashé le même firmware plusieurs fois?
Votre poêle est-il ancien? La version du firmware de votre carte Fumis est-elle ancienne? S'agit-il d'une Alpha 65?
Quelle modification software avez-vous faite afin que cela fonctionne?

Palyndiel, 2024-11-03:
Bonjour,
J'ai re-flashé plusieurs fois la version 3.1.11.
Le poêle est récent, modèle Turbo Fonte de 2020.
Aucune modification du firmware, j'ai simplement ajouté des logs pour tenter de debuguer.

J'ai maintenant un nouveau problème, le boitier m'indique qu'il est bien connecté au poêle et à MQTT, mais dans home assistant, la connexion ne cesse de sauté :
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
En gris déconnecté et en jaune connecté.
Du coup le pilotage via HA n'est pas possible. Peut être faut-il ouvrir un autre ticket pour ce problème.

Domochip, 2024-11-03:
Votre poêle a-t-il une prise RJ12 accessible ou bien un splitter a dû être ajouté?
Désolé, mais je persiste à croire à un problème matériel.
Que vous affiche la page web du module durant les périodes "Déconnecté"?

Palyndiel, 2024-11-03:
Oui je suis branché à une prise rj12 accessible directement à l’arrière de l’appareil.
Le module m’affiche toujours connecté, même lorsque je suis déconnecté.

Domochip, 2024-11-03:
Connaissez-vous le modèle de la carte mère de votre poêle?

arabine, 2024-11-03:
Bonjour, j'ai réussi à réparer le module en suivant les conseils du vendeur : comme indiqué ci-dessus, j'ai repassé un coup de fer à souder sur toutes les pattes des composants et ça a fonctionné !

Voilà merci domochip en tout cas pour ta disponibilité et le projet.

Domochip, 2024-11-10:
Bonjour @Palyndiel
J'ai relu ce ticket et j'avais omis un point intéressant:
_Je n’arrive plus à faire fonctionner le module palacontrol avec mon poêle Turbo Fonte. Le boîtier fonctionnait encore en début d’année_

Concernant un problème software:
- de nombreux utilisateurs du WPalaControl ne rencontre pas ce soucis
- si cela fonctionnait bien en début d'année, pourriez-vous retester avec le firmware que vous aviez à ce moment là?
- afin de vérifier que la communication au poêle est opérationnelle, il faut l'interroger: envoyer une commande GET+TMPS par exemple

La source la plus probable du problème reste à mon sens un défaut de soudure sur le si8621.
On appelle ça une soudure sèche (ou aussi soudure collée). Il y a un infime espace entre la patte et la piste sur le PCB. Au début, il y a contact, puis avec le temps, il devient intermittent et finalement il n'y a plus de contact.
La difficulté vient du fait qu'en appuyant sur la patte du composant avec un multimètre pour vérifier la continuité, cela fait contact… puis quand on la relâche le problème revient…
C'est pour cela que je vérifie au microscope que c'est correctement soudé.

Bonne Journée

Palyndiel, 2024-11-12:
Bonjour, la connexion au poêle est stable depuis le 8 novembre. Plus de connexion/déconnexion intempestive. Sans aucune modification de ma part, juste en laissant le module branché.
Je vais néanmoins investir dans un kit de soudure, et essayer de ressouder le composant que vous m’indiquez si jamais je rencontre à nouveau des soucis.
En attendant je clôture le ticket pour ne pas vous embêter plus longtemps.
Merci du temps accordé.

Palyndiel, 2024-11-12:
Bonjour, la connexion au poêle est stable depuis le 8 novembre. Plus de connexion/déconnexion intempestive. Sans aucune modification de ma part, juste en laissant le module branché.
Je vais néanmoins investir dans un kit de soudure, et essayer de ressouder le composant que vous m’indiquez si jamais je rencontre à nouveau des soucis.
En attendant je clôture le ticket pour ne pas vous embêter plus longtemps.
Merci du temps accordé.

Closed 2024-11-12.

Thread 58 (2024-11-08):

SetPoint unknown in Home Assistant

tanc, 2024-11-08:
Hi, I just received my box this morning, nice easy set up, thanks!

The only issue I have is that the SETP isn't registering in Home Assistant and is showing as unknown.
This is what MQTT Explorer says is showing:

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

```
{
  "~": "WPalaControl",
  "availability": {
    "topic": "~/connected",
    "value_template": "{{ iif(int(value) > 0, 'online', 'offline') }}"
  },
  "command_template": "SET+SETP+{{ value }}",
  "command_topic": "~/cmd",
  "device": {
    "configuration_url": "http://wpalacontrol.local",
    "identifiers": [
      "WPalaControl_LT201829880571372127806"
    ],
    "model": "83",
    "name": "Stove",
    "sw_version": "47 (2023-01-30)",
    "via_device": "WPalaControl_3494548E2B82"
  },
  "device_class": "temperature",
  "min": 17,
  "max": 23,
  "mode": "slider",
  "name": "SetPoint",
  "object_id": "stove_setp",
  "state_topic": "~/SETP",
  "unique_id": "WPalaControl_LT201829880571372127806_SETP",
  "unit_of_measurement": "°C",
  "value_template": "{{ value_json.SETP }}"
}
```

Looking at this could it be that the min/max are wrong? This stove is a hydro/boiler model (Ginger Idro 15) so the SetPoint is much higher as its setting the water temperature. Its min is 65 and max 80.

Also `RoomTemp` on this model should be `WaterTemp` with `"name": "Water Temperature",`

Domochip, 2024-11-08:
Hi,

Could you go to this page :
[http://wpalacontrol.local/cgi-bin/sendmsg.lua?cmd=GET+STDT](http://wpalacontrol.local/cgi-bin/sendmsg.lua?cmd=GET+STDT)
and give me the values of:
- FLUID
- SPLMIN
- SPLMAX

tanc, 2024-11-08:
```
"FLUID": 1,
"SPLMIN": 65,
"SPLMAX": 80,
```

Domochip, 2024-11-14:
Could you compile from the master branch and confirm it works fine for you, please

Domochip, 2024-11-15:
It's available in the last release

Closed 2024-11-15.

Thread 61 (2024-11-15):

Feature request: Expose the firebox temp to Home Assistant

tanc, 2024-11-15:
For my nerdy graph needs it would be great to expose the T3 temp to Home Assistant so that I can monitor the relationship between the tank temp and the firebox temp.

```
{
    "INFO": {
        "CMD": "GET TMPS",
        "RSP": "OK"
    },
    "DATA": {
        "T1": 71.9, <-- Tank or outflow temp
        "T2": 63.9, <-- Inflow temp
        "T3": 210, <-- Firebox temp
        "T4": 0,
        "T5": 18 <-- Room temp
    },
    "SUCCESS": true
}
```

Domochip, 2024-11-16:
It's added in the current master branch as a disabled by default one

BorisNanev, 2024-11-16:
"T3": 210, <-- Firebox temp is important for monitoring how stove works and when exhaust gases go too much UP is indicator that your stove is for cleaning (i mean inside of waste box).

tanc, 2024-11-16:
> It's added in the current master branch as a disabled by default one

Should I be able to see it and enable it in Home Assistant already? Or do you mean it needs to be enabled in code first?

BorisNanev, 2024-11-16:
i cant see it in HA. only in browser of domochip.

Domochip, 2024-11-17:
@BorisNanev It is in master branch not part of the current release. You need to compile and flash it in your module if you want to see it

@tanc it will be created in Home Assistant but you'll need to go to the device and enable this entity, then you'll be able to use it like any other

Domochip, 2024-11-17:
going to the stove device, you can find some grayed out sensors, and enable them :
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

BorisNanev, 2024-11-17:
I know, I enabled all sensors in home assistant but I don't have T3. I can a see it in browser but not in hove assistant .

Domochip, 2024-11-17:
You'll find the version containing these new sensors in the latest pre-release (3.4.0)
https://github.com/Domochip/WPalaControl/releases

BorisNanev, 2024-11-17:
That's awesome. Thanks one more time. I was looking for this from years. :)

Domochip, 2024-11-19:
@tanc @BorisNanev Does everything looks good for you?
I'm considering switch the current pre-release as release

BorisNanev, 2024-11-19:
I don't have any issues with pre-release. Everything works perfectly. I do have some random disconnects for 2-3 seconds 3-4 time per day, same as stable release.(I think it's not from bad WiFi connection coz router and device show good connection). It's not big of deal for me.

Domochip, 2024-11-20:
@BorisNanev thank you for the feeback.
Regarding the disconnection, I have it sometime and sometime not (3 days without it on my side now...)
I was not able to catch it yet.
Could you confirm me this behavior :
 - in Home assistant, both Stove and WPalaControl connectivity disconnect and reconnect
 - in WPalaControl webpage, the UpTime is not resetted

BorisNanev, 2024-11-20:
Yes, I can confirm. 35 hours without disconnection. I didn't check UpTime but I will next time.

Domochip, 2024-11-20:
ok, I'll close this issue.
Regarding the disconnection, it is still very hard to figure out now.
I'll have a look at this later when I've time.

tanc, 2024-11-21:
Sorry I wasn't able to test, but just wanted to say thanks, I did the update today and can confirm the fluegas sensor is now available (after enabling it)

Closed 2024-11-20.

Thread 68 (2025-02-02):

WPalaControl unstable

abcklaus, 2025-02-02:
Hi,

I am using the WPalaControl with Palazzetti "Marianne" stove. For any reason the WPalaControl seems to be unstable.

The uptime in the status indicates that the device is restarting. In this example the uptime is about 2h. Actually the last power cycle is about 20h ago ...

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

In Home Assistant I am using the Palazzetti integration. Also here I am observing availability issues:

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

I other issues I have seen that the power supply may be a problem. But after trying three different power supplies I am pretty sure that this is not the root cause.

Any Idea what I can do?

Thanks

Michael

Domochip, 2025-02-03:
Hi,

This may happen if there is some Wifi connectivity issue.
What is the percentage next to your wifi network in Config page?

abcklaus, 2025-02-03:
It’s 58%. Distance between access point and Domochip is about 5m.

abcklaus, 2025-02-03:
ok, thank you. I didn't expect that the quality of the wifi connection may cause issues like that.

In the meantime I did some tweaks in my environment and will observe.

abcklaus, 2025-02-06:
I did some tweaks in my wifi environment. The quality is now between 90 and 100%

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

Today in the morning (07:40) I see that the uptime is again just 2h. Means that the device has restarted at about 05:00

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

Is the wifi connection still an issue?

Domochip, 2025-02-07:
Hi,

Before going more in technical research, is it possible for you to use the MQTT integration (native for this module)?
I want to clarify if that come from HTTP endpoints or not

abcklaus, 2025-02-07:
ok, no problem. I have deactivated the Palazzetti integration in HomeAssistant and activated the MQ integration.

abcklaus, 2025-02-11:
The MQTT Integration is active for some days now.

But there is no improvement. The uptime is still just some hours. The max value I have seen is 1d.

In HA the stove becomes unavailable from time to time.

Domochip, 2025-02-23:
Hi,

Sorry I was off these last two weeks.
mm, sounds like an hardware problem.
Which WPalaControl HW version do you have (1.1 or 2.0) (it's written on the box and on the PCB).
Did you build it yourself or bought it ready to use and where?

abcklaus, 2025-02-23:
Hi,

I am using Version 2.0.

Domochip, 2025-03-03:
Have you bought it from me or from DIYPala?

abcklaus, 2025-03-04:
I bought it from you. Order number is  #515307

Domochip, 2025-03-05:
ok
Do you see a kind of pattern of the restart?
Next steps would be to monitor via USB from a computer and flash some test firmware (going deeper then).
Is it something you are comfortable with? otherwise a return/refund is always possible.

abcklaus, 2025-03-06:
Hi,
yes, flashing some firmware is no problem. I am familiar with that.

I have here an Lolin D1 mini from another project. What do you think - is it worth to flash your firmware to check if the issue is located in the other D1 mini?

Domochip, 2025-03-06:
yes, can be a good first test.

abcklaus, 2025-03-06:
I used a Lolin D1 Mini v4.0. I have compiled and flashed the firmware with vscode/platform io. For and reason this device seems not to be compatible. As soon as i have connected my stove, the stove Shows the error E0004.
So I moved back to the original D1 mini.

abcklaus, 2025-03-07:
ok, found the reason why my D1 mini is not working. The pins are soldered on the other side of the board.

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

abcklaus, 2025-03-07:
ok, found a workaround ;-)

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

Let's see how the new D1 mini will behave ...

abcklaus, 2025-03-22:
During the last days I have monitored the device. Unfortunately switching the D1mini did not help. I am observing the instability. In most cases the device does not have an uptime larger than several hours.

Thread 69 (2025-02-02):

Stove im Home Assistant

abcklaus, 2025-02-02:
Hi,

I am using the WPalaControl with Palazzetti "Marianne" stove. I am using WPalaControl with Palazzetti integration in Home Assistant.

I have observed that the stove becomes unavailable in HA if the target temperature is change while the stove is powered off:

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

Is that behavior intended?

Thanks

Michael

Domochip, 2025-02-03:
Hi,

Do you mean the target temperature is changed directly on the stove physically or via HA?

abcklaus, 2025-02-03:
It happens when I change the target temp in HA.

Domochip, 2025-02-03:
Interesting,
could you give it a try directly using HTTP command and check that it disconnect or not (ex: set target temperature to 20):
http://{WPalaControlIP}/cgi-bin/sendmsg.lua?cmd=SET+SETP+20

abcklaus, 2025-02-03:
Response for HTTP command:

{"INFO":{"CMD":"SET SETP","RSP":"OK"},"DATA":{"SETP":20.00},"SUCCESS":true}

One more thing: When setting the temp in HA I get this error:

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

abcklaus, 2025-02-03:
After executing the HTTP command WPalaControl remains available. But it takes some seconds (approximately 10s) to reflect the change in HA.

Ok, I will contact dotav.

Domochip, 2025-02-03:
For the 10sec delay, it is normal, Palazzetti integration is using HTTP endpoints and no notification is sent from WPalaControl nor CBox using this protocol.
What's interesting is that HA didn't considered the WPalaControl has disconnected, so yes, the problem is coming from Palazzetti integration

dotvav, 2025-02-03:
Hi there. It could be that the response payload from WPalaControl has a
format that I was not expecting. If the processing throws an exception
(missing attribute, unexpected type...) then the device will be reported as
unavailable, until it responds again with something that fulfills the
expectations. Which could be 10s. I haven't had a chance to test today, but
I have some doubts about SETP returning a float value instead of an int.
I'll check tomorrow.

Le lun. 3 févr. 2025, 16:35, Domochip ***@***.***> a écrit :

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

Domochip, 2025-02-03:
Nice trail found. If my memory is good, some stove are able to be configured with 0.2°C step, but in that case, i don't know what CBox returns...

Domochip, 2025-03-05:
@dotvav were you able to confirm if it comes from the float returned?

dotvav, 2025-03-05:
Hi, I came back from vacation last week and haven't found the time to run these tests. I will look into that in the coming days.

dotvav, 2025-03-09:
I ran some tests today, both on the HA integration and on the API lib, and the `float` type of SETP does not cause any issues.

@abcklaus, can you open an issue on the HA Core Github? It will get assigned to me. I don't want to polute Domochip's repo. Feel free to link to this issue and share the tests that you have performed. Also, any error message ort information you can get from the HA logs would be very helpful.

abcklaus, 2025-03-09:
ok, done.

#140215

Thanks

dotvav, 2025-03-10:
@Domochip below is the relevant error from @abcklaus's logs. There is a imeout error when I call `GET STDT`. Do you think that it is possible that the WPalaControl could struggle with concurrent http requests if HA is calling `GET STDT` right after (or during) the `SET SETP` command? (I'll also try to understand why I call `GET STDT` at this point)

````
2025-03-09 18:16:44.569 ERROR (MainThread) [homeassistant.components.palazzetti] Communication error
Traceback (most recent call last):
  File "/usr/local/lib/python3.13/site-packages/aiohttp/connector.py", line 1116, in _wrap_create_connection
    sock = await aiohappyeyeballs.start_connection(
           ^^^^^^^^^^^^^^^^^^^^^^^^^^^^^^^^^^^^^^^^
    ...<5 lines>...
    )
    ^
  File "/usr/local/lib/python3.13/site-packages/aiohappyeyeballs/impl.py", line 73, in start_connection
    sock = await _connect_sock(
           ^^^^^^^^^^^^^^^^^^^^
    ...<6 lines>...
    )
    ^
  File "/usr/local/lib/python3.13/site-packages/aiohappyeyeballs/impl.py", line 208, in _connect_sock
    await loop.sock_connect(sock, address)
  File "/usr/local/lib/python3.13/asyncio/selector_events.py", line 641, in sock_connect
    return await fut
           ^^^^^^^^^
asyncio.exceptions.CancelledError

The above exception was the direct cause of the following exception:

Traceback (most recent call last):
  File "/usr/local/lib/python3.13/site-packages/aiohttp/client.py", line 703, in _request
    conn = await self._connector.connect(
           ^^^^^^^^^^^^^^^^^^^^^^^^^^^^^^
        req, traces=traces, timeout=real_timeout
        ^^^^^^^^^^^^^^^^^^^^^^^^^^^^^^^^^^^^^^^^
    )
    ^
  File "/usr/local/lib/python3.13/site-packages/aiohttp/connector.py", line 548, in connect
    proto = await self._create_connection(req, traces, timeout)
            ^^^^^^^^^^^^^^^^^^^^^^^^^^^^^^^^^^^^^^^^^^^^^^^^^^^
  File "/usr/local/lib/python3.13/site-packages/aiohttp/connector.py", line 1056, in _create_connection
    _, proto = await self._create_direct_connection(req, traces, timeout)
               ^^^^^^^^^^^^^^^^^^^^^^^^^^^^^^^^^^^^^^^^^^^^^^^^^^^^^^^^^^
  File "/usr/local/lib/python3.13/site-packages/aiohttp/connector.py", line 1411, in _create_direct_connection
    raise last_exc
  File "/usr/local/lib/python3.13/site-packages/aiohttp/connector.py", line 1380, in _create_direct_connection
    transp, proto = await self._wrap_create_connection(
                    ^^^^^^^^^^^^^^^^^^^^^^^^^^^^^^^^^^^
    ...<7 lines>...
    )
    ^
  File "/usr/local/lib/python3.13/site-packages/aiohttp/connector.py", line 1113, in _wrap_create_connection
    async with ceil_timeout(
               ~~~~~~~~~~~~^
        timeout.sock_connect, ceil_threshold=timeout.ceil_threshold
        ^^^^^^^^^^^^^^^^^^^^^^^^^^^^^^^^^^^^^^^^^^^^^^^^^^^^^^^^^^^
    ):
    ^
  File "/usr/local/lib/python3.13/asyncio/timeouts.py", line 116, in __aexit__
    raise TimeoutError from exc_val
TimeoutError

The above exception was the direct cause of the following exception:

Traceback (most recent call last):
  File "/usr/local/lib/python3.13/site-packages/pypalazzetti/client.py", line 402, in _execute_command
    async with self._session.get(request_url) as response:
               ~~~~~~~~~~~~~~~~~^^^^^^^^^^^^^
  File "/usr/local/lib/python3.13/site-packages/aiohttp/client.py", line 1425, in __aenter__
    self._resp: _RetType = await self._coro
                           ^^^^^^^^^^^^^^^^
  File "/usr/local/lib/python3.13/site-packages/aiohttp/client.py", line 707, in _request
    raise ConnectionTimeoutError(
        f"Connection timeout to host {url}"
    ) from exc
aiohttp.client_exceptions.ConnectionTimeoutError: Connection timeout to host http://10.60.20.10/cgi-bin/sendmsg.lua?cmd=GET+STDT

The above exception was the direct cause of the following exception:

Traceback (most recent call last):
  File "/usr/src/homeassistant/homeassistant/components/palazzetti/config_flow.py", line 31, in async_step_user
    await client.connect()
  File "/usr/local/lib/python3.13/site-packages/pypalazzetti/client.py", line 48, in connect
    r = await self._execute_command(
        ^^^^^^^^^^^^^^^^^^^^^^^^^^^^
    ...<2 lines>...
    )
    ^
  File "/usr/local/lib/python3.13/site-packages/pypalazzetti/client.py", line 409, in _execute_command
    raise CommunicationError("API communication error") from ex
pypalazzetti.exceptions.CommunicationError: API communication error
`````

Domochip, 2025-03-10:
That's interesting.
Could be a good idea that I give it a try because we are currently working on a reliability problem with @abcklaus .
To clarify things, the first post mention that this problem occurs when changing the temperature (setPoint) while the stove is off.
Does it also happens when the stove is on?

@dotvav  Even if this is something you can fix, I want to give it a try to understand if this is a memory shortage or a "simple" watchdog timeout. (I can improve things for watchdog timeout)

abcklaus, 2025-03-10:
Yes, the issue occurs only if the stove is turned off.

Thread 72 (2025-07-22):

F4L does not appear in Home Assistant via MQTT

quenting57, 2025-07-22:
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

Hi,

My stove has a ducted output. When I physically change the fan speed of the ducted output on the stove, the F4L value updates correctly on the web interface.

However, F4L does not appear in Home Assistant via MQTT, unlike other controls such as temperature, power level, etc.

I’d like to integrate this F4L value into Home Assistant like the other MQTT entities.
Is it possible to expose it, or is there a specific configuration needed?

I’ve attached two screenshots:
	•	Home Assistant interface (F4L missing)
	•	Stove’s web interface (F4L visible and updating)

Thanks!

quenting57, 2025-07-28:
I have noticed that the F4L value is properly published in the MQTT topic PalazettiControl/FAND in JSON format, for example :
`{"F1V":0,"F2V":0,"F1RPM":0,"F2L":2,"F2LF":0,"F3S":0.00,"F4S":0.00,"F3L":0,"F4L":5}`

quenting57, 2025-07-28:
Meanwhile, my Home Assistant solution :

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

And synchronized with a Home Assistant input_number using automations.
**We need to find out why F4L wasn’t automatically discovered by Home Assistant**.

Domochip, 2025-07-31:
The only condition for FAN4 to appear is: FAN2TYPE > 2
This is true in your case, so something is weird here
if you connect to your MQTT broker using MQTT Explorer, do you find a retained message on a topic like : homeassistant/number/WPalaControl_LTXXXX_FAN4 OR homeassistant/switch/WPalaControl_LTXXXX_FAN4?

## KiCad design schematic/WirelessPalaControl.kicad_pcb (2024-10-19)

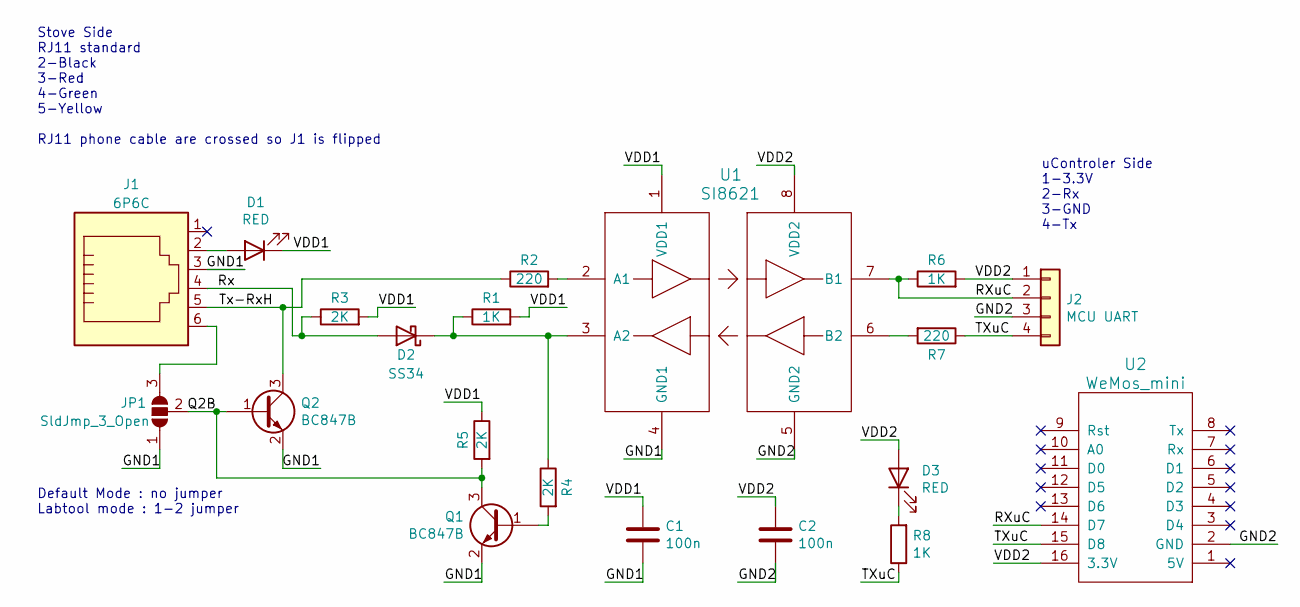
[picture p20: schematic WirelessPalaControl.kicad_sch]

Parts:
C1, C2: 100n; C_0805_2012Metric_Pad1.15x1.40mm_HandSolder
D1, D3: RED; LED_0805_2012Metric_Pad1.15x1.40mm_HandSolder
D2: SS34; D_SMA
J1: 6P6C; Ali_RJ12
J2: MCU UART; PinHeader_1x04_P2.54mm_Vertical
JP1: SldJmp_3_Open; SolderJumper-3_P1.3mm_Open_Pad1.0x1.5mm_NumberLabels
Q1, Q2: BC847B; SOT-23_Handsoldering
R1, R6, R8: 1K; R_0805_2012Metric_Pad1.15x1.40mm_HandSolder
R2, R7: 220; R_0805_2012Metric_Pad1.15x1.40mm_HandSolder
R3, R4, R5: 2K; R_0805_2012Metric_Pad1.15x1.40mm_HandSolder
U1: SI8621; SOIC-8_3.9x4.9mm_P1.27mm
U2: WeMos_mini; wemos-d1-mini-DIL-only

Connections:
/GND1: C1.2, J1.3, JP1.1 (A), Q1.2 (E), Q2.2 (E), U1.4 (GND1)
/GND2: C2.2, J2.3, U1.5 (GND2), U2.2 (GND)
/Q2B: JP1.2 (C), Q1.3 (C), Q2.1 (B), R5.2
/RXuC: J2.2, R6.1, U1.7 (B1), U2.14 (D7)
/Rx: D2.2 (A), J1.4, R3.1
/TXuC: J2.4, R7.1, R8.1, U2.15 (D8)
/Tx-RxH: J1.5, Q2.3 (C), R2.1
/VDD1: C1.1, D1.1 (K), R1.2, R3.2, R5.1, U1.1 (VDD1)
/VDD2: C2.1, D3.2 (A), J2.1, R6.2, U1.8 (VDD2), U2.16 (3.3V)
unnamed: D1.2 (A), J1.2
unnamed: D2.1 (K), R1.1, R4.1, U1.3 (A2)
unnamed: D3.1 (K), R8.2
unnamed: J1.6, JP1.3 (B)
unnamed: Q1.1 (B), R4.2
unnamed: R2.2, U1.2 (A1)
unnamed: R7.2, U1.6 (B2)

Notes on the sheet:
uControler Side 1-3.3V 2-Rx 3-GND 4-Tx
Default Mode : no jumper Labtool mode : 1-2 jumper
Stove Side RJ11 standard 2-Black 3-Red 4-Green 5-Yellow RJ11 phone cable are crossed so J1 is flipped

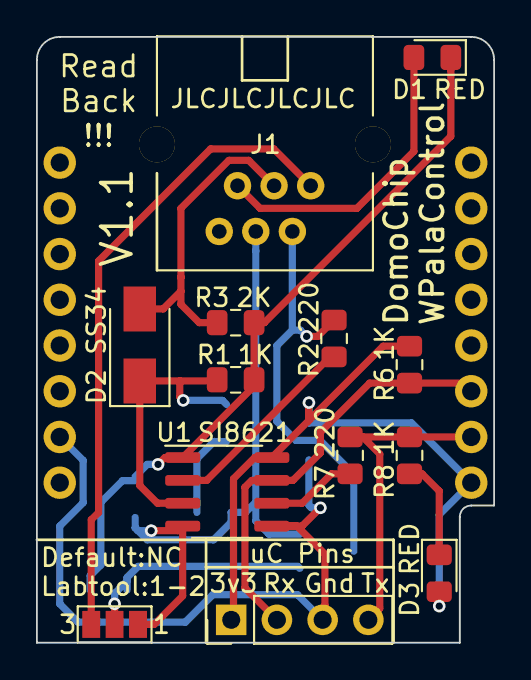
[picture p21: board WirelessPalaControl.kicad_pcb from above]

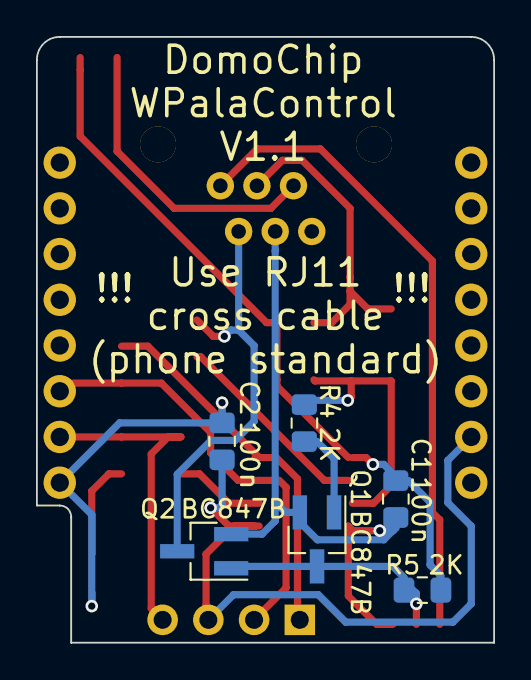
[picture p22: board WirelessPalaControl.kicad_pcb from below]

Board: 2 copper layers, 25.4 x 33.7 mm, 20 parts (7 on the bottom side), 16 nets.

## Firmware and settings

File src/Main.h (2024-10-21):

#ifndef Main_h
#define Main_h

#include <Arduino.h>

// Helper macros to convert a define to a string
#define STRINGIFY(x) #x
#define TOSTRING(x) STRINGIFY(x)

// ----- Should be modified for your application -----
#define APPLICATION1_MANUFACTURER "Domochip"
#define APPLICATION1_MODEL "WPalaControl"
#define APPLICATION1_CLASS WPalaControl
#define VERSION_NUMBER "3.1.11"

#define APPLICATION1_NAME TOSTRING(APPLICATION1_CLASS)     // stringified class name
#define APPLICATION1_HEADER TOSTRING(APPLICATION1_CLASS.h) // calculated header file "{APPLICATION1_NAME}.h"
#define DEFAULT_AP_SSID APPLICATION1_NAME                  // Default Access Point SSID "{APPLICATION1_NAME}{4 digits of ChipID}"
#define DEFAULT_AP_PSK APPLICATION1_NAME "Pass"            // Default Access Point Password "{APPLICATION1_NAME}Pass"

// Control EventSourceMan code (To be used by Application if EventSource server is needed)
#define EVTSRC_ENABLED 1
#define EVTSRC_MAX_CLIENTS 2
#define EVTSRC_KEEPALIVE_ENABLED 0

// Enable developper mode (SPIFFS editor)
#define DEVELOPPER_MODE 0

// Log Serial Object
#ifdef ESP8266
#define LOG_SERIAL Serial1
#else
#define LOG_SERIAL Serial
#endif
// Choose Log Serial Speed
#define LOG_SERIAL_SPEED 38400

// Choose Pin used to boot in Rescue Mode
// #define RESCUE_BTN_PIN 2

// Define time to wait for Rescue press (in s)
// #define RESCUE_BUTTON_WAIT 3

// Status LED
// #define STATUS_LED_SETUP pinMode(XX, OUTPUT);pinMode(XX, OUTPUT);
// #define STATUS_LED_OFF digitalWrite(XX, HIGH);digitalWrite(XX, HIGH);
// #define STATUS_LED_ERROR digitalWrite(XX, HIGH);digitalWrite(XX, HIGH);
// #define STATUS_LED_WARNING digitalWrite(XX, HIGH);digitalWrite(XX, HIGH);
// #define STATUS_LED_GOOD digitalWrite(XX, HIGH);digitalWrite(XX, HIGH);

// construct Version text
#if DEVELOPPER_MODE
#define VERSION VERSION_NUMBER "-DEV"
#else
#define VERSION VERSION_NUMBER
#endif

#endif

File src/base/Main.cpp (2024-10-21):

#ifdef ESP8266
#include <ESP8266WiFi.h>
#include <ESP8266WebServer.h>
using WebServer = ESP8266WebServer;
#else
#include <WiFi.h>
#include <WebServer.h>
#endif
#include <EEPROM.h>
#include <LittleFS.h>
#include <FS.h>

#include "Version.h"
#include "../Main.h"
#include "Application.h"
#include "Core.h"
#include "WifiMan.h"

// include Application header file
#include APPLICATION1_HEADER

// WebServer
WebServer server(80);
// flag to pause application Run during Firmware Update
bool pauseApplication = false;
// variable used by objects to indicate system reboot is required
bool shouldReboot = false;

// System
Core core('0', "Core");

// WifiMan
WifiMan wifiMan('w', "WiFi");

// Application1 object
APPLICATION1_CLASS application1('1', APPLICATION1_NAME);

//-----------------------------------------------------------------------
// Setup function
//-----------------------------------------------------------------------
void setup()
{
#ifdef LOG_SERIAL
  LOG_SERIAL.begin(LOG_SERIAL_SPEED);
  LOG_SERIAL.println();
  LOG_SERIAL.println();
  LOG_SERIAL.flush();
#endif

#ifdef STATUS_LED_SETUP
  STATUS_LED_SETUP
#endif
#ifdef STATUS_LED_ERROR
  STATUS_LED_ERROR
#endif

#ifdef LOG_SERIAL
  LOG_SERIAL.print(F(APPLICATION1_MANUFACTURER " " APPLICATION1_MODEL " "));
  LOG_SERIAL.println(VERSION);
  LOG_SERIAL.println(F("---Booting---"));
#endif

#ifndef RESCUE_BUTTON_WAIT
#define RESCUE_BUTTON_WAIT 3
#endif

  bool skipExistingConfig = false;

  // look into EEPROM for Rescue mode flag
  EEPROM.begin(4);
  skipExistingConfig = EEPROM.read(0) != 0;
  if (skipExistingConfig)
    EEPROM.write(0, 0);
  EEPROM.end();

#ifdef RESCUE_BTN_PIN
  // if config already skipped, don't wait for rescue button
  if (!skipExistingConfig)
  {
#ifdef LOG_SERIAL
    LOG_SERIAL.print(F("Wait Rescue button for "));
    LOG_SERIAL.print(RESCUE_BUTTON_WAIT);
    LOG_SERIAL.println(F(" seconds"));
#endif

    pinMode(RESCUE_BTN_PIN, (RESCUE_BTN_PIN != 16) ? INPUT_PULLUP : INPUT);
    for (int i = 0; i < 100 && skipExistingConfig == false; i++)
    {
      if (digitalRead(RESCUE_BTN_PIN) == LOW)
        skipExistingConfig = true;
      delay(RESCUE_BUTTON_WAIT * 10);
    }
  }
#endif

#ifdef LOG_SERIAL
  if (skipExistingConfig)
  {
    LOG_SERIAL.println(F("-> RESCUE MODE : Stored configuration won't be loaded."));
  }
#endif
#ifdef ESP8266
  if (!LittleFS.begin())
#else
  if (!LittleFS.begin(true))
#endif
  {
#ifdef LOG_SERIAL
    LOG_SERIAL.println(F("/!\\   File System Mount Failed   /!\\"));
    LOG_SERIAL.println(F("/!\\ Configuration can't be saved /!\\"));
#endif
  }

  // Init Core
  core.init(skipExistingConfig);

  // Init WiFi
  wifiMan.init(skipExistingConfig);

  // Init Application
  application1.init(skipExistingConfig);

#ifdef LOG_SERIAL
  LOG_SERIAL.print(F("Start WebServer : "));
#endif
  core.initWebServer(server, shouldReboot, pauseApplication);
  wifiMan.initWebServer(server, shouldReboot, pauseApplication);
  application1.initWebServer(server, shouldReboot, pauseApplication);

  server.begin();
#ifdef LOG_SERIAL
  LOG_SERIAL.println(F("OK"));

  LOG_SERIAL.println(F("---End of setup()---"));
#endif
}

//-----------------------------------------------------------------------
// Main Loop function
//-----------------------------------------------------------------------
void loop(void)
{

  // Handle WebServer
  server.handleClient();

  if (!pauseApplication)
  {
    application1.run();
  }

  wifiMan.run();

  if (shouldReboot)
  {
#ifdef LOG_SERIAL
    LOG_SERIAL.println("Rebooting...");
    delay(100);
    LOG_SERIAL.end();
#endif
    ESP.restart();
  }
}

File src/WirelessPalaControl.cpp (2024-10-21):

#include "WirelessPalaControl.h"

#ifdef ESP8266
#define PALA_SERIAL Serial
#else
#define PALA_SERIAL Serial2
#endif

// Serial management functions -------------
int WPalaControl::myOpenSerial(uint32_t baudrate)
{
#ifdef ESP8266
  PALA_SERIAL.begin(baudrate);
  PALA_SERIAL.pins(15, 13); // swap ESP8266 pins to alternative positions (D7(GPIO13)(RX)/D8(GPIO15)(TX))
#else
  PALA_SERIAL.begin(baudrate, SERIAL_8N1, 23, 5); // set ESP32 pins to match hat position (IO23(RX)/IO5(TX))
#endif
  return 0;
}
void WPalaControl::myCloseSerial()
{
  PALA_SERIAL.end();
  // set TX PIN to OUTPUT HIGH to avoid stove bus blocking
#ifdef ESP8266
  pinMode(15, OUTPUT);
  digitalWrite(15, HIGH);
#else
  pinMode(5, OUTPUT);
  digitalWrite(5, HIGH);
#endif
}
int WPalaControl::mySelectSerial(unsigned long timeout)
{
  size_t avail;
  unsigned long startmillis = millis();
  while ((avail = PALA_SERIAL.available()) == 0 && (startmillis + timeout) > millis())
    ;

  return avail;
}
size_t WPalaControl::myReadSerial(void *buf, size_t count) { return PALA_SERIAL.read((char *)buf, count); }
size_t WPalaControl::myWriteSerial(const void *buf, size_t count) { return PALA_SERIAL.write((const uint8_t *)buf, count); }
int WPalaControl::myDrainSerial()
{
  PALA_SERIAL.flush(); // On ESP, Serial.flush() is drain
  return 0;
}
int WPalaControl::myFlushSerial()
{
  PALA_SERIAL.flush();
  while (PALA_SERIAL.read() != -1)
    ; // flush RX buffer
  return 0;
}
void WPalaControl::myUSleep(unsigned long usecond) { delayMicroseconds(usecond); }

void WPalaControl::mqttConnectedCallback(MQTTMan *mqttMan, bool firstConnection)
{

  // Subscribe to needed topic
  // prepare topic subscription
  String subscribeTopic = _ha.mqtt.generic.baseTopic;

  // Replace placeholders
  MQTTMan::prepareTopic(subscribeTopic);

  switch (_ha.mqtt.type) // switch on MQTT type
  {
  case HA_MQTT_GENERIC:
  case HA_MQTT_GENERIC_JSON:
  case HA_MQTT_GENERIC_CATEGORIZED:
    subscribeTopic += F("cmd");
    break;
  }

  if (firstConnection)
    mqttMan->publish(subscribeTopic.c_str(), ""); // make empty publish only for firstConnection
  mqttMan->subscribe(subscribeTopic.c_str());

  // raise flag to publish Home Assistant discovery data
  _needPublishHassDiscovery = true;
}

void WPalaControl::mqttDisconnectedCallback()
{
  // if MQTT is disconnected, MQTT Reconnection will publish "1" to connectedTopic
  _publishedStoveConnected = false;
}

void WPalaControl::mqttCallback(char *topic, uint8_t *payload, unsigned int length)
{
  // if topic is basetopic/cmd
  // commented because only this topic is subscribed

  String cmd;
  String strJson;

  // convert payload to String cmd
  cmd.concat((char *)payload, length);

  // replace '+' by ' '
  cmd.replace('+', ' ');

  // execute Palazzetti command
  executePalaCmd(cmd, strJson, true);

  // publish json result to MQTT
  String baseTopic = _ha.mqtt.generic.baseTopic;
  MQTTMan::prepareTopic(baseTopic);
  String resTopic(baseTopic);
  resTopic += F("result");
  _mqttMan.publish(resTopic.c_str(), strJson.c_str());
}

void WPalaControl::publishStoveConnectedToMqtt(bool stoveConnected)
{
  if (_mqttMan.connected() && _publishedStoveConnected != stoveConnected)
  {
    // if Stove is connected, publish 2 to connected topic otherwise fallback to 1
    _mqttMan.publishToConnectedTopic((stoveConnected ? "2" : "1"));
    _needPublishHassDiscovery = true; // raise flag to publish Home Assistant discovery data
    _publishedStoveConnected = stoveConnected;
  }
}

bool WPalaControl::publishDataToMqtt(const String &baseTopic, const String &palaCategory, const JsonDocument &jsonDoc)
{
  bool res = false;
  if (_mqttMan.connected())
  {
    if (_ha.mqtt.type == HA_MQTT_GENERIC)
    {
      // for each key/value pair in DATA
      for (JsonPairConst kv : jsonDoc["DATA"].as<JsonObjectConst>())
      {
        // prepare topic
        String topic(baseTopic);
        topic += kv.key().c_str();
        // publish
        res = _mqttMan.publish(topic.c_str(), kv.value().as<String>().c_str());
      }
    }

    if (_ha.mqtt.type == HA_MQTT_GENERIC_JSON)
    {
      // prepare topic
      String topic(baseTopic);
      topic += palaCategory;
      // serialize DATA to JSON
      String serializedData;
      serializeJson(jsonDoc["DATA"], serializedData);
      // publish
      res = _mqttMan.publish(topic.c_str(), serializedData.c_str());
    }

    if (_ha.mqtt.type == HA_MQTT_GENERIC_CATEGORIZED)
    {
      // prepare category topic
      String categoryTopic(baseTopic);
      categoryTopic += palaCategory;
      categoryTopic += '/';

      // for each key/value pair in DATA
      for (JsonPairConst kv : jsonDoc["DATA"].as<JsonObjectConst>())
      {
        // prepare topic
        String topic(categoryTopic);
        topic += kv.key().c_str();
        // publish
        res = _mqttMan.publish(topic.c_str(), kv.value().as<String>().c_str());
      }
    }
  }
  return res;
}
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

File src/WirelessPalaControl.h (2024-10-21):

#ifndef WirelessPalaControl_h
#define WirelessPalaControl_h

#include "Main.h"
#include "base/MQTTMan.h"
#include "base/EventSourceMan.h"
#include "base/Application.h"

const char appDataPredefPassword[] PROGMEM = "ewcXoCt4HHjZUvY1";

#include "data/status1.html.gz.h"
#include "data/config1.html.gz.h"

#include <Palazzetti.h>
#include <WiFiUdp.h>

class WPalaControl : public Application
{
private:
#define HA_MQTT_GENERIC 0
#define HA_MQTT_GENERIC_JSON 1
#define HA_MQTT_GENERIC_CATEGORIZED 2

  typedef struct
  {
    byte type = HA_MQTT_GENERIC_JSON;
    uint32_t port = 1883;
    char username[32 + 1] = {0};
    char password[64 + 1] = {0};
    struct
    {
      char baseTopic[64 + 1] = {0};
    } generic;
    bool hassDiscoveryEnabled = true;
    char hassDiscoveryPrefix[32 + 1] = {0};
  } MQTT;

#define HA_PROTO_DISABLED 0
#define HA_PROTO_MQTT 1

  typedef struct
  {
    byte protocol = HA_PROTO_DISABLED;
    char hostname[64 + 1] = {0};
    uint16_t uploadPeriod = 60;
    MQTT mqtt;
  } HomeAutomation;

  HomeAutomation _ha;
  int _haSendResult = 0;
  WiFiClient _wifiClient;
  MQTTMan _mqttMan;
  EventSourceMan _eventSourceMan;
  WiFiUDP _udpServer;

  Palazzetti _Pala;
  unsigned long _lastAllStatusRefreshMillis = 0;

  bool _needPublish = false;
  Ticker _publishTicker;
  bool _publishedStoveConnected = false;
  bool _needPublishHassDiscovery = false;

  int myOpenSerial(uint32_t baudrate);
  void myCloseSerial();
  int mySelectSerial(unsigned long timeout);
  size_t myReadSerial(void *buf, size_t count);
  size_t myWriteSerial(const void *buf, size_t count);
  int myDrainSerial();
  int myFlushSerial();
  void myUSleep(unsigned long usecond);

  void mqttConnectedCallback(MQTTMan *mqttMan, bool firstConnection);
  void mqttDisconnectedCallback();
  void mqttCallback(char *topic, uint8_t *payload, unsigned int length);
  void publishStoveConnectedToMqtt(bool stoveConnected);
  bool publishDataToMqtt(const String &baseTopic, const String &palaCategory, const JsonDocument &jsonDoc);
  bool publishHassDiscoveryToMqtt();
  bool executePalaCmd(const String &cmd, String &strJson, bool publish = false);

  void publishTick();
  void udpRequestHandler(WiFiUDP &udpServer);

  void setConfigDefaultValues();
  bool parseConfigJSON(JsonDocument &doc, bool fromWebPage);
  String generateConfigJSON(bool forSaveFile);
  String generateStatusJSON();
  bool appInit(bool reInit);
  const PROGMEM char *getHTMLContent(WebPageForPlaceHolder wp);
  size_t getHTMLContentSize(WebPageForPlaceHolder wp);
  void appInitWebServer(WebServer &server, bool &shouldReboot, bool &pauseApplication);
  void appRun();

public:
  WPalaControl(char appId, String fileName);
};

#endif

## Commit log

2019-11-03 temperature function renamed
2019-11-04 V0.6 Add PowerLevel and RoomFan management
2019-11-06 Add WDT Feed to prevent reboot
    [WirelessPalaControl.cpp]
2019-11-09 Fix Set Room Fan
    [WirelessPalaControl.cpp]
2020-01-05 Add schematic V1.0
    [WirelessPalaControl.kicad_pcb, WirelessPalaControl.sch]
2020-01-12 Update schematic
    [WirelessPalaControl.kicad_pcb, WirelessPalaControl.sch]
2020-01-21 Update schematic fix rj12
    [WirelessPalaControl.kicad_pcb]
2020-01-26 Update PCB fix size V1.1
    [WirelessPalaControl.kicad_pcb]
2020-03-10 Add Box
    [WirelessPalaControl Box.stl, WirelessPalaControl Lid.stl, WirelessPalaControl v9.f3d]
2020-11-30 Add Power Level to MQTT order
2021-01-13 V1.2.5 Up version for Power Level MQTT
2021-10-21 V1.2.7 Up version for counters and timers MQTT cmd
2021-12-27 Modify HTTP GET error messages
    [WirelessPalaControl.cpp]
2021-12-28 Modify HTTP GET error messages #2
    [WirelessPalaControl.cpp]
2021-12-28 Modify HTTP GET error messages #3
    [WirelessPalaControl.cpp]
2022-01-02 Add PUMP to ALLS
2022-01-07 Fix error messages text
    [WirelessPalaControl.cpp]
2022-01-28 Slightly increase box connector hole size
    [WirelessPalaControl v10.f3d, WirelessPalaControl v9.f3d]
2022-02-26 Update box stl
    [WirelessPalaControl Box.stl, WirelessPalaControl Lid.stl]
2022-02-26 Fix Websocket STOVE_DATETIME sent as int
    [WirelessPalaControl.cpp]
2023-11-19 Fix version of ArduinoJson lib temporarily
2023-11-19 Ensure correct float rendering
    [WirelessPalaControl.cpp]
2023-11-19 Use more ArduinoJson in executePalaCmd
2023-12-09 Switch LOG_SERIAL to 38400 for simplicity
2023-12-09 Switch monitor_speed to 38400
2023-12-09 Fix Stack issue by passing the whole jsonDoc
    [WirelessPalaControl.cpp, WirelessPalaControl.h]
2023-12-09 Use the last ArduinoJson library
2023-12-09 Fix GET LABL result
    [WirelessPalaControl.cpp]
2023-12-12 Add RSP ERROR answers
    [WirelessPalaControl.cpp]
2023-12-12 revert code simplification for GET PARM
    [WirelessPalaControl.cpp]
2023-12-16 new WirelessBase files
2023-12-16 Replace AsyncWebServer by ESP8266WebServer in function definitions
    [WirelessPalaControl.cpp, WirelessPalaControl.h]
2023-12-17 WirelessBase Format
2023-12-17 Replace ESPAsyncUDP by WiFiUDP
    [WirelessPalaControl.cpp, WirelessPalaControl.h]
2023-12-17 WirelessBase Update
2023-12-19 Switch strings to Flash
2023-12-19 switch publishDataToMqtt to if structure for memory
2023-12-20 Fix missing proper convertion for executePalaCmd return
    [WirelessPalaControl.cpp]
2023-12-20 not Using FlashString with ArduinoJson saves a LOT of stack
2023-12-20 last ArduinoJson object named with FlashString
2023-12-20 last ArduinoJson object named with FlashString bis
2023-12-20 Fix udp Packet reading not working
    [WirelessPalaControl.cpp]
2023-12-21 WirelessBase update V2.0.0
2023-12-22 Update WirelessBase to 2.1.0
2023-12-28 Update WirelessBase to 2.1.1
2023-12-28 Fix build on !Windows
    - use / as path separator, not \
    - use proper capitalization for include names
    [Main.cpp, Main.h, WirelessPalaControl.h]
2024-01-03 Move "PublishTick" Serial print
2024-01-04 Update WirelessBase to 2.1.2
2024-01-04 Update WirelessBase to 2.1.3
2024-01-04 Update WirelessBase to 2.1.4
2024-01-10 Change Stove device information
2024-01-10 Add Power entity
2024-02-03 Add Room temperature entity
2024-02-03 Update WirelessBase to 2.1.5
2024-02-03 Adapt code for ArduinoJson7
2024-02-03 Fix icon of Room fan in HASS
    [WirelessPalaControl.cpp]
2024-02-11 Fix Hass wrong Power topic
    [WirelessPalaControl.cpp]
2024-09-01 Update WirelessBase to 2.2.0
2024-09-01 Update WirelessBase to 2.2.1
2024-09-01 Add platformio esp32 platform
2024-09-01 Replace ESP8266WebServer to WebServer
    [WirelessPalaControl.cpp, WirelessPalaControl.h]
2024-09-01 Replace server.keepAlive(false); with SERVER_KEEPALIVE_FALSE() macro
    [WirelessPalaControl.cpp]
2024-09-01 Adapt publishTicker attach
2024-09-02 adapt LOG_SERIAL for ESP32
2024-09-02 Draft of Serial mgmt for ESP32
2024-09-07 Update WirelessBase to 2.2.2
2024-09-13 Update WirelessBase to 2.2.3
2024-09-24 Adjust Fan presence order
2024-09-25 Fix bad topic in HA autodiscovery
    [WirelessPalaControl.cpp]
2024-09-25 Update WirelessBase to 2.2.4
2024-09-25 define correct return target topic for SET commands
    [WirelessPalaControl.cpp]
2024-09-28 Update WirelessBase to 2.3.0
2024-09-28 Update WirelessBase to 2.3.1
2024-09-28 Increase ESP32 upload speed
2024-09-28 Switch to JSON post for config
2024-09-29 Define ArduinoJson lib version
2024-09-29 Reorder AppRun actions to avoid double publishTick
    [WirelessPalaControl.cpp]
2024-10-01 Update WirelessBase to 2.3.2 - Simplify Version number
2024-10-01 Update WirelessBase to 2.3.3
2024-10-03 Update WirelessBase to 2.3.4
2024-10-06 Update WirelessBase to 2.3.5
2024-10-09 Update WirelessBase to 2.3.6
2024-10-12 Update WirelessBase to 2.3.7
2024-10-16 Update WirelessBase to 2.3.8
2024-10-19 Update schematic to KiCAD8
    [WirelessPalaControl.kicad_pcb, WirelessPalaControl.kicad_sch, WirelessPalaControl.sch]
2024-10-19 Add gitignore for KiCad
2024-10-19 Update WirelessBase to 2.3.9
2024-10-20 Update WirelessBase to 2.3.10
2024-10-21 Rename files from WirelessPalaControl to WPalaControl
2024-10-21 Update WirelessBase to 2.3.11
